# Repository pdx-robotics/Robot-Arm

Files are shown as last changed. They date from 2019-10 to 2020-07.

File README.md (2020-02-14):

# Robot-Arm
This repo is for the Robot Arm project by the Viking Robotics Society.

## Introduction
The idea of this project is to build a 5-DOF Robot Arm that will be able to draw and manipulate tasks. This project is set out to be completed by the end of the Winter Term 2020. A backup deadline is Spring 2020.

## Terminology

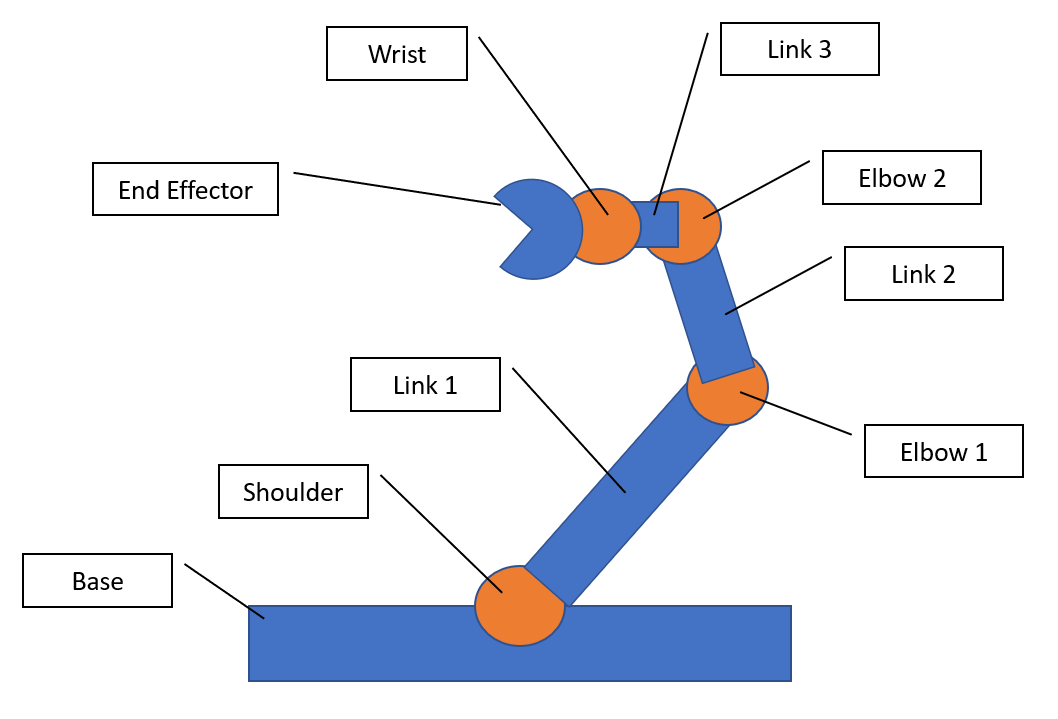
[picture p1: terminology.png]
Robot Arm Terminology


## Current Progress

Version 2

Version 2

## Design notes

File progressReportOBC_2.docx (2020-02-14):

To: OBC Committee

From: Viking Robotics Society

Subject: Robot Arm – Progress Report 2

Dear OBC Committee,

The following letter is to report on the progress of the Robot Arm project that is due at the end of Spring

term 2020.

Project website: https://pdx-robotics.github.io/Robot-Arm/

Introduction

On November 01, 2019, we have submitted the project proposal for designing a Robotic Arm for the

Viking Robotics Society. Upon receiving approval for the project, we have immediately started working

on designing the CAD model and planning for the project. The goal is to build a fully functional robotic

arm that can draw and write from human user input. The project is currently being worked on by the

members of VRS until the final submission.

The Background

VRS does not have a working robot that is designed and programmed by the members from scratch. All

of our previous projects have been from pre-built kits. We currently have several members who are

seniors and very invested in learning more about robotics. This project is initiated to give the members the

opportunities to learn more about the engineering design process and nurture a new generation of new

members about project management and teamwork. This project will also give the club something to

show off that is of our own design.

Work Completed

Physical Design

We have completed the second design of the robot arm, which has been 3D printed. However, this current design is too heavy to perform smooth motions; the next design aims at reducing the weight and improve the rigidity of the joints.

Electronics

We have assembled the Dynamixel motors and performed torque tests to evaluate their functionality. The AX12’s perform as expected. The RX64 is using an obsolete communication protocol that does not have sufficient documentation. We have consulted with Professor Alexander Hunt, who works with Dynamixels in his research. Dr. Hunt said that he has never worked on the old protocol in his line of work, given many years of experience with Dynamixel. We will need to order a new motor that uses the lastest communication protocol for the robot arm project.

Show & tell

Video

Link 1 (https://www.youtube.com/watch?v=8Y9AhXR_reE)

Link 2 (https://www.youtube.com/watch?v=c67NiDEWrtY)

Picture

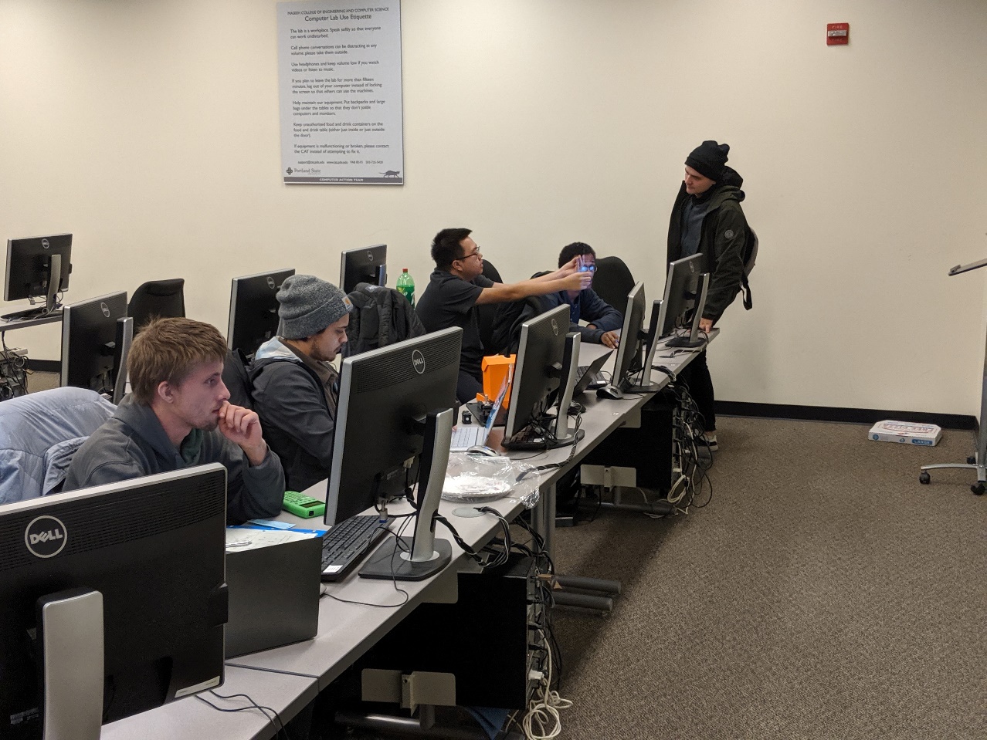
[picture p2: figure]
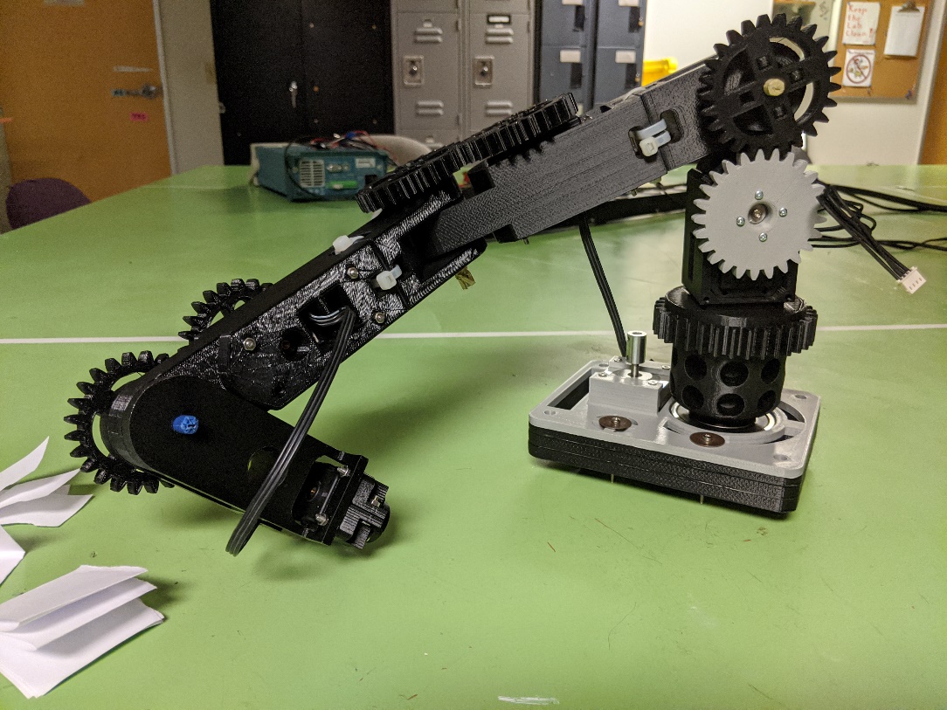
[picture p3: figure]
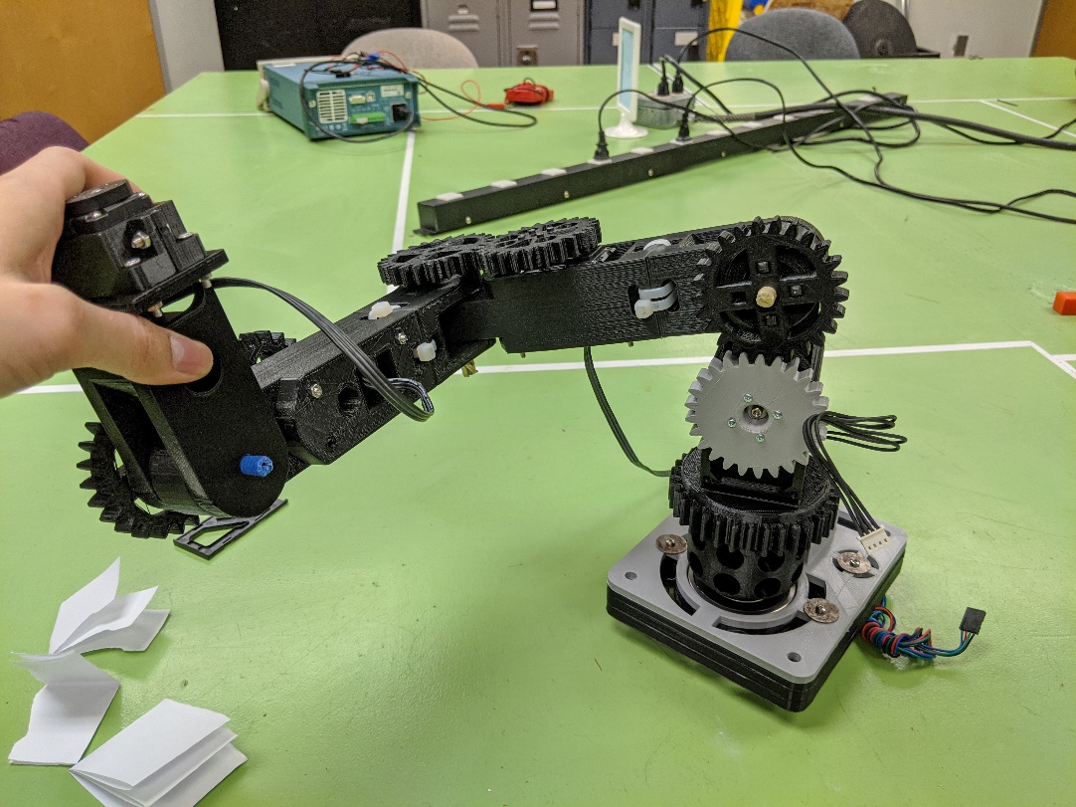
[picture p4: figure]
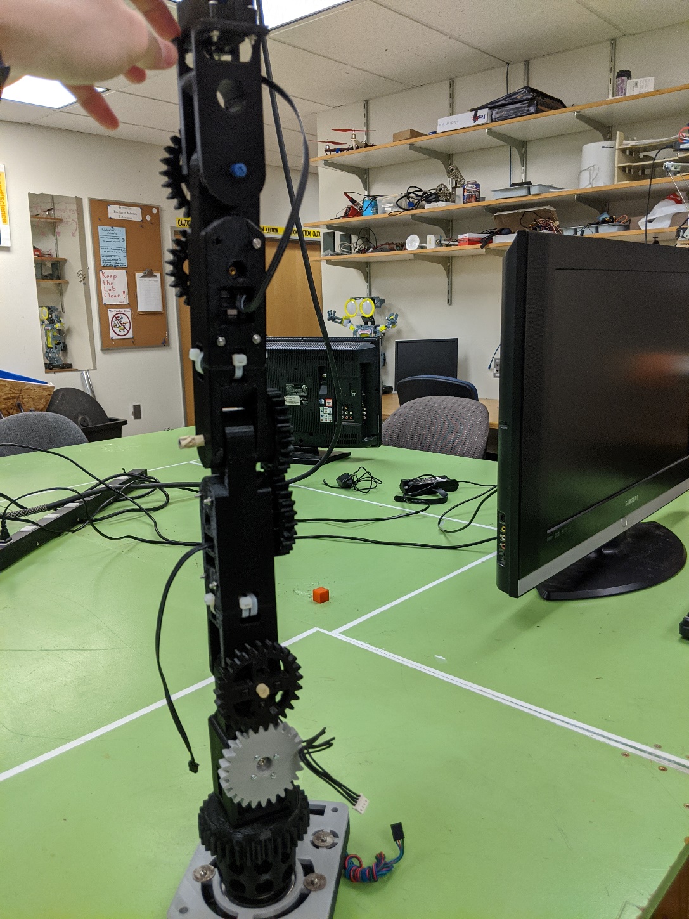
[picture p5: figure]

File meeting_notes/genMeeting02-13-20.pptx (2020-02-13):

## Robot Arm Update

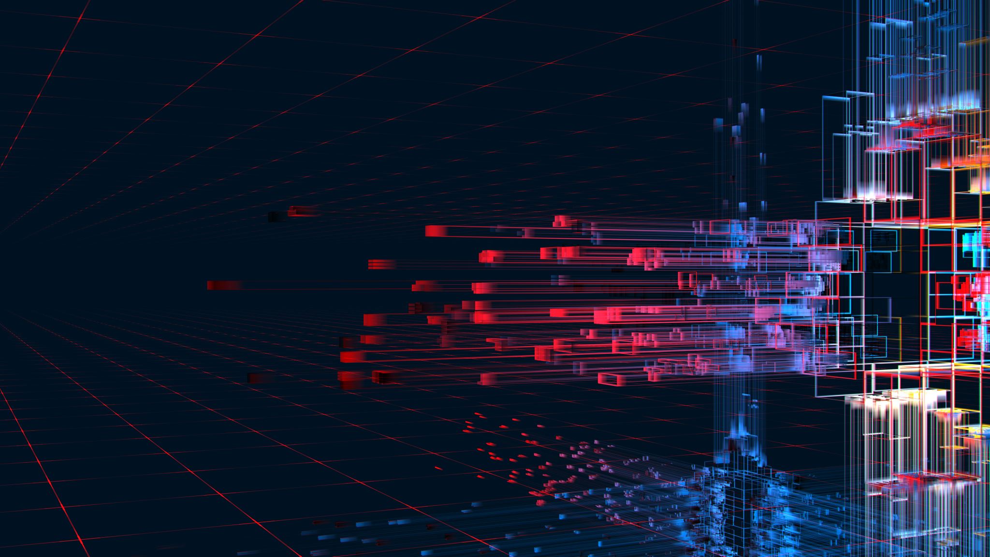
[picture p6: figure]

Viking Robotics Society

## Update from the programming team

- Issues?
- Roadblock?
- How’s the CM700 board? Did you make an progress on it?

## Update for the base redesign

- Is it print-ready?
- Any issues?

## Current arm

- The base shaft fractured. We will have to reprint it.

## Timeline revisiting

- The base redesign needed to be done by the end of this term.
- Might need to rethink the timeline for the programming group.

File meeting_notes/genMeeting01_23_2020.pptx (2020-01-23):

## Robot arm weekly meeting

Viking Robotics Society
Thursday 01-16-2020

## Current Progress

- We did things.
- The AX12 can move the base around.
- We got the RX64 to work. It spins around
- The term is getting busy, if you need to take a break to do your school stuff, you are more than welcome to.

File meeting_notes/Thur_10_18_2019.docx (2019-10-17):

Thursday, October 10, 2019 @ 5:00pm

Review of previous meeting:

- Github training
- Any question about Github or deadlines?

Goals for today meeting:

- Welcome our technical adviser, updates on current progress.

Agenda:

- Current progress of the arm:
  - Finished the base design
  - Finished Shoulder Gear
- Give the Cody our current overall design of the arm
  - Feedback from Cody?

Question?

Next meeting?

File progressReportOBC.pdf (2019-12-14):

To: OBC Committee

From: Viking Robotics Society

Subject: Robot Arm – Progress Report

Dear OBC Committee,

The following letter is to report on the progress of the Robot Arm project that is due at the end of Spring term 2020.

Introduction

On November 01, 2019, we have submitted the project proposal for designing a Robotic Arm for the Viking Robotics Society. Upon receiving approval for the project, we have immediately started working on designing the CAD model and planning for the project. The goal is to build a fully functional robotic arm that can draw and write from human user input. The project is currently being worked on by the members of VRS until the final submission.

The Background

VRS does not have a working robot that is designed and programmed by the members from scratch. All of our previous projects have been from pre-built kits. We currently have several members who are seniors and very invested in learning more about robotics. This project is initiated to give the members the opportunities to learn more about the engineering design process and nurture a new generation of new members about project management and teamwork. This project will also give the club something to show off that is of our own design.

Work Completed

We have completed the second iteration of the arm design and we are currently printing out more parts to start the assembly. We have also received several servos and parts that we ordered. A team is currently working on the communication and electronics of the arm. We have also been in constant contact with the Agile and Adaptive Robotics Lab graduate student to get help with the technical and challenges that we encountered in the process.

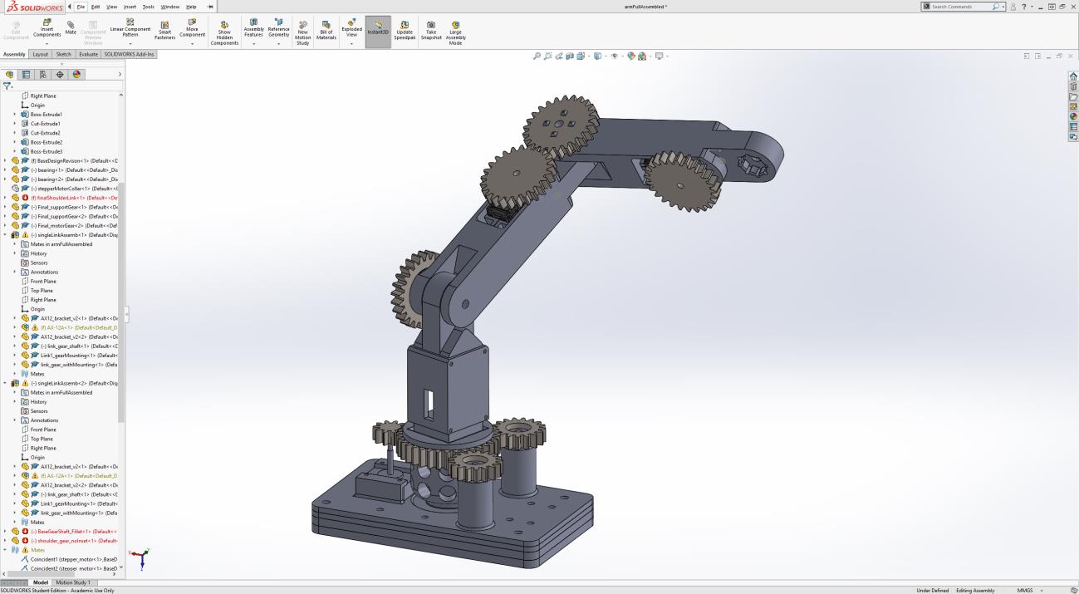
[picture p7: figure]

Work to Be Completed

We plan to have the full assembly by the end of the Winter Break; this will be the second version of the arm. During the Winter term and Spring term, the software team can start working on the programming of the arm, while the design team will work on the electronics and continuously making improvements upon the current model. We also plan to show off our current progress at the Robotics Club game night to recruit more members to help with the project.

Anticipated Problems

One of the servos that we ordered on November 12, 2019, has not shown up. We plan to have the full assembly to be completed during the Winter break. If we do not get the servo in time, the deadline for the project will be delayed. Additionally, the OBC committee will not be available during the break, which makes ordering replacement for the servo will be significantly challenging. I have contacted the advisor of the club to look into this issue and make sure that we will get the part in time.

The 3D printer of the club is degrading. It has broken down many times when we tried to print the parts. The parts have also been warping much more significantly than normal, which causes fitting to be challenging. We are designing our model to be 3D-printing friendly, but without a good printer, it is taking significantly longer to get parts. We will have to work with what we have. We will try to maintain the printer and fix it if necessary.

Conclusion

Based on the current progress, we should have the project to be completed at the end of the Spring term 2020. Despite several delays in our timeline, we are still on schedule. We plan to order several more parts that we have missed in the last order to support the project.

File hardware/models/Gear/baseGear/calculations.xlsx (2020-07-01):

Driving gear calculation for the bas
 | d (pich diameter) mm | 58.3
 | N (number of teeth) | 11
 | a (Addendum) | 5.3 | Addendum Circle | 63.6
 | b (Dedendum) | 6.625 | Dedendum Circle | 51.675
 | m (mod) | 5.3 | Base Circle | 59.76445068
 | P (diametral pitch) | 0.1886792453 | Pitch Circle | 58.3
 | hk (working depth) | 11.925

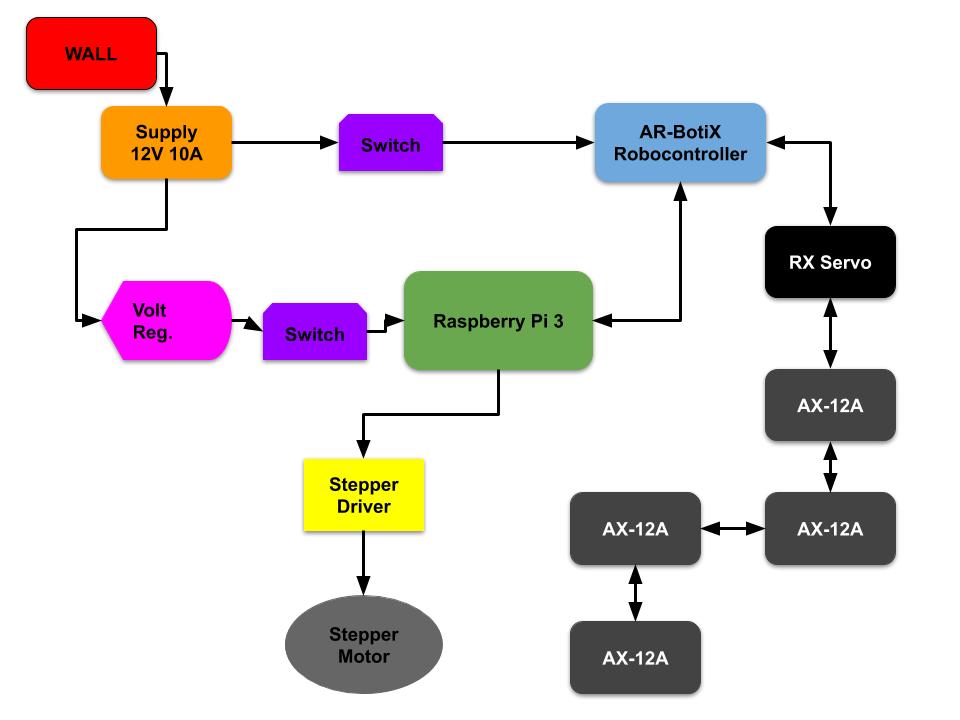
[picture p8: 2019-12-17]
Electronics Schematics/VRS_Arm_CircuitOutline.jpg

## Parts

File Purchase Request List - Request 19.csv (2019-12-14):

Click to return to INDEX | Viking Robotics Society
Provide a backup purchase link for all purchases. Requests take a while to process and parts may run out of stock during the process
Budget Request #: | 19 | Date Submitted: | 12/2/2019 | Date Approved: | WIP
Notes | This budget request is for VRS game night |  |  | Amount Approved: | $0.00
 |  |  | Preferred Purchase Option |  |  |  |  |  |  | Backup Purchase Option
Reason for Purchase | Items | Notes | Count in one order | # of orders to get | Cost per order | S&H | Total w/ S&H | Link | Notes | Count in one order | # of orders to get | Cost per order | S&H | Total w/ S&H | Link | Notes
Overall Total |  |  |  |  |  | $13.15 | $185.53 |  |  | Overall Total |  |  | $0.00 | $0.00
Robot Arm project | CM-700 Robot Controller |  | 1 | 1 | $119.90 | $13.15 | $133.05 | https://www.trossenrobotics.com/store/p/6410-CM-700-Robotis-Servo-Controller.aspx
Robot Arm project | LN-101 USB Downloader |  | 1 | 1 | $14.90 | $0.00 | $14.90 | https://www.trossenrobotics.com/store/p/6322-LN-101-USB-Downloader.aspx
Robot Arm project | Filament 1.75mm - Black |  | 1 | 1 | $17.59 | $0.00 | $17.59 | https://www.amazon.com/HATCHBOX-3D-Filament-Dimensional-Accuracy/dp/B00J0ECR5I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
Robot Arm project | Filament 3.00mm - Yellow |  | 1 | 1 | $19.99 | $0.00 | $19.99 | https://www.amazon.com/HATCHBOX-3D-Filament-Dimensional-Accuracy/dp/B019EFB7Y4?s=industrial

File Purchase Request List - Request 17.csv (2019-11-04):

Click to return to INDEX | Viking Robotics Society
Provide a backup purchase link for all purchases. Requests take a while to process and parts may run out of stock during the process
Budget Request #: | Request 17 | Date Submitted: | 10/28/2019 | Date Approved: | 11/01/2019
Notes | This purchase request is for the Robot Arm project |  |  | Amount Approved: | $510.50
 |  |  | Preferred Purchase Option |  |  |  |  |  |  | Backup Purchase Option
Reason for Purchase | Items | Notes | Count in one order | # of orders to get | Cost per order | S&H | Total w/ S&H | Link | Notes | Count in one order | # of orders to get | Cost per order | S&H | Total w/ S&H | Link | Notes
Overall Total |  |  |  |  |  | $24.46 | $510.50 |  |  | Overall Total |  |  | $0.00 | $0.00
Robot Arm Project | Raspberry Pi 3 |  | 1 | 1 | $57.89 |  | $57.89 | https://www.amazon.com/ELEMENT-Element14-Raspberry-Pi-Motherboard/dp/B07P4LSDYV
Robot Arm Project | Ar-BotiX-M Robo Controller |  | 1 | 1 | $39.95 |  | $39.95 | https://www.trossenrobotics.com/p/arbotix-robot-controller.aspx
Robot Arm Project | Stepper Motor Controller |  | 5 | 1 | $9.99 |  | $9.99 | https://www.amazon.com/KINGPRINT-DRV8825-Stepper-Driver-Printer/dp/B075XH1TSJ?s=industrial
Robot Arm Project | Dynamixel AX-12A Digital Servos |  | 1 | 2 | $44.90 | $13.14 | $102.94 | https://www.trossenrobotics.com/dynamixel-ax-12-robot-actuator.aspx
Robot Arm Project | Dynamixel Cables |  | 10 | 1 | $14.90 |  | $14.90 | https://www.trossenrobotics.com/p/250mm-3-pin-dynamixel-compatible-cables-10-pack
Robot Arm Project | Power Supply |  | 1 | 1 | $21.99 |  | $21.99 | https://www.amazon.com/Xenocam-Power-Supply-Splitter-Cameras/dp/B07X5LQ17L
Robot Arm Project | Dynamixel RX |  | 1 | 1 | $195.93 | $3.32 | $199.25 | http://www.robotis.us/dynamixel-rx-64-hn05-n1/
Robot Arm Project | 3D printing filament |  | 1 | 1 | $19.99 |  | $19.99 | https://www.amazon.com/HATCHBOX-3D-Filament-Dimensional-Accuracy/dp/B00J0ECR5I
Robot Arm Project | Bearing |  | 1 | 1 | $35.60 | $8.00 | $43.60 | https://www.mcmaster.com/2349K425

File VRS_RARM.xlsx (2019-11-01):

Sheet: RESOURCES
RESOURCES | LINK
How - To | https://www.raspberryturk.com/details/arm/python-dynamixel.html
Stepper Motor | https://www.youtube.com/watch?v=5CmjB4WF5XA

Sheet: Electronics BOM
ITEM | QUANTITY | LINK | COST ($) Individual | In Inventory
Raspberry Pi 3 | 1 | https://www.amazon.com/ELEMENT-Element14-Raspberry-Pi-Motherboard/dp/B07P4LSDYV | 51.89 | NO
Ar-BotiX-M Robo Controller | 1 | https://www.trossenrobotics.com/p/arbotix-robot-controller.aspx | 39.95 | NO
Stepper Motor Controller | 1 | https://www.amazon.com/KINGPRINT-DRV8825-Stepper-Driver-Printer/dp/B075XH1TSJ?s=industrial |  | NO
Dynamixel AX-12A Digital Servos | 2 | https://www.trossenrobotics.com/dynamixel-ax-12-robot-actuator.aspx | 44.9 | NO
JK42HS48 - 1604A | 0 | https://www.amazon.com/STEPPERONLINE-Stepper-Bipolar-Connector-compatible/dp/B00PNEQKC0 | 13.99 | YES
Dynamixel Cables | 1 | https://www.trossenrobotics.com/p/250mm-3-pin-dynamixel-compatible-cables-10-pack | 14.9 | NO
Power Supply | 1 | https://www.amazon.com/Xenocam-Power-Supply-Splitter-Cameras/dp/B07X5LQ17L | 21.99 | NO
Dynamixel RX | 1 | http://www.robotis.us/dynamixel-rx-64-hn05-n1/ | 195.33 | NO

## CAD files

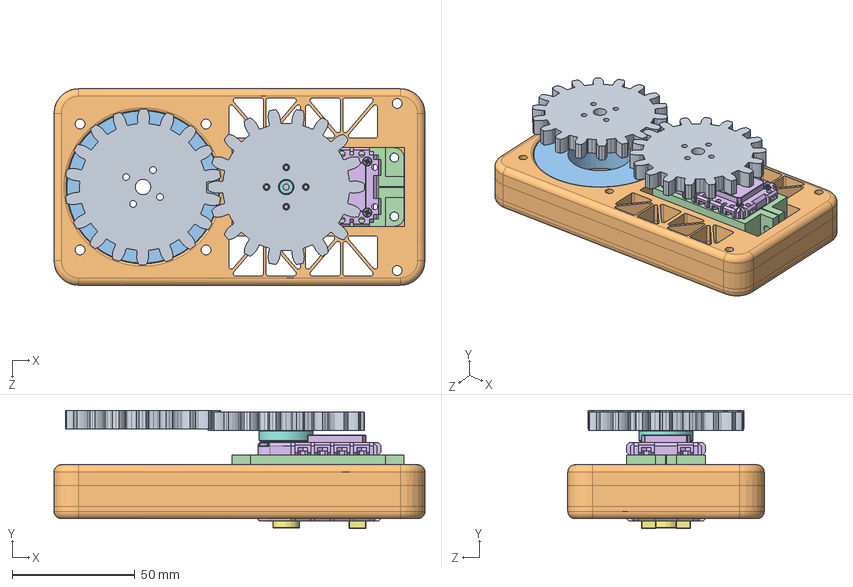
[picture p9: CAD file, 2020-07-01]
hardware/models/assembledArm/assemblyCheck/fullAssembly_v2.SLDASM
151.0 x 48.1 x 80.0 mm
baseGear x 2
base_v2
largeBearing
AX12_bracket_v2 x 2
AX-12A-01
AX-12A-02
AX-12A-03
AX-12A-04
SetScrew x 4

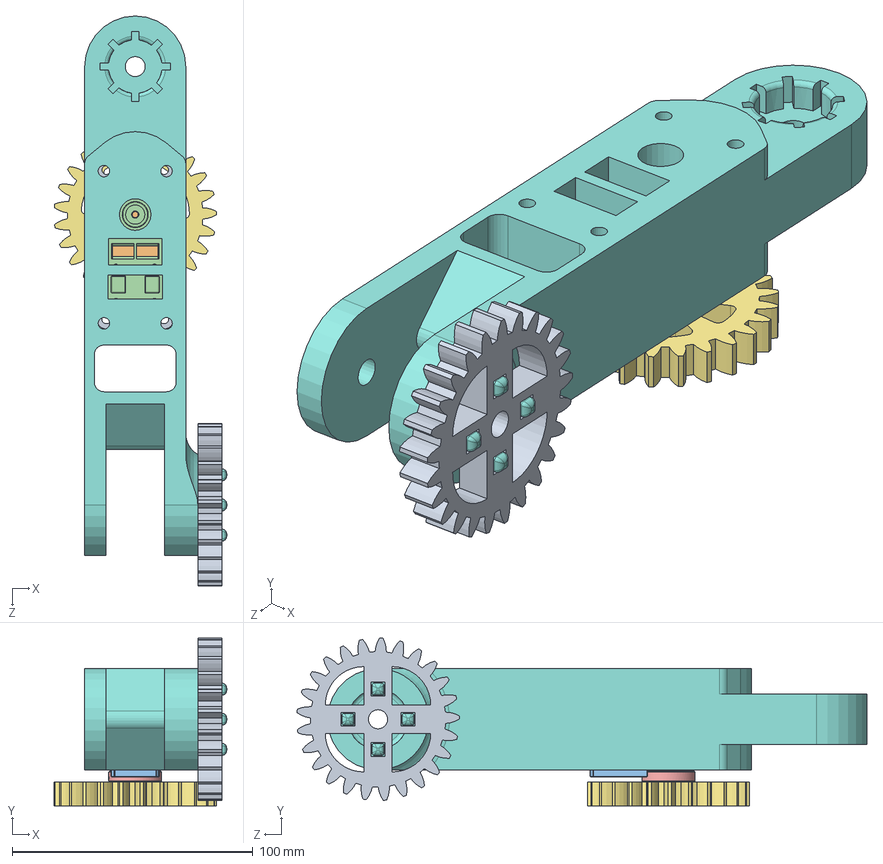
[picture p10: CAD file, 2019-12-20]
hardware/models/assembledArm/link_1_2/singleLinkAssemb.SLDASM
71.6 x 69.7 x 236.6 mm
AX12_bracket_v2 x 2
AX-12A-01
AX-12A-02
AX-12A-03
AX-12A-04
SetScrew x 4
link_gear_shaft
Link1_gearMounting
link_gear_withMounting

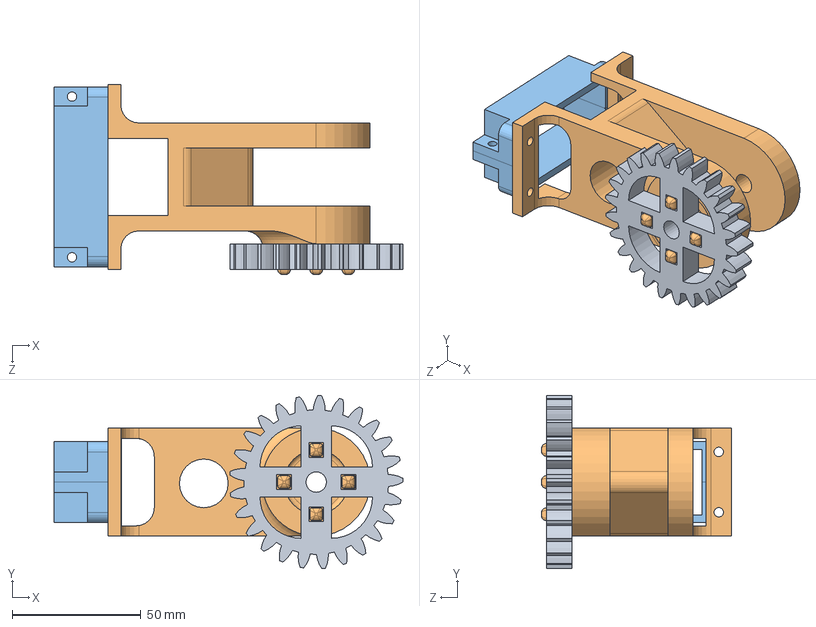
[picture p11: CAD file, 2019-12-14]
hardware/models/assembledArm/linkWrist/wristAssembly.SLDASM
135.7 x 67.4 x 74.0 mm
link_gear_withMounting
wristLinkRevision
AX12_bracket_v2 x 2

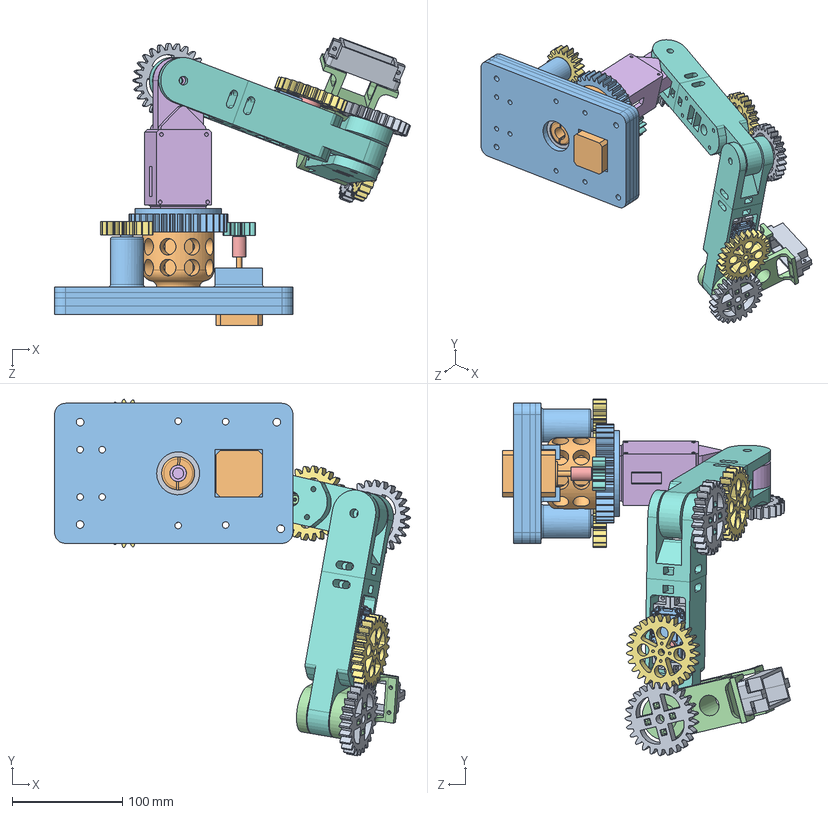
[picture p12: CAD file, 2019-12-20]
hardware/models/assembledArm/assemblyCheck/armFullAssembled.SLDASM
322.4 x 322.9 x 260.9 mm
largeBearing
stepper_motor
BaseDesignRevison
bearing x 2
finalShoulderLink
Final_supportGear x 2
Final_motorGear
AX12_bracket_v2 x 6
AX-12A-01 x 2
AX-12A-02 x 2
AX-12A-03 x 2
AX-12A-04 x 2
SetScrew x 8
link_gear_shaft x 2
Link1_gearMounting x 2
link_gear_withMounting x 3
BaseGearShaft_Fillet
shoulder_gear_noInset
wristLinkRevision

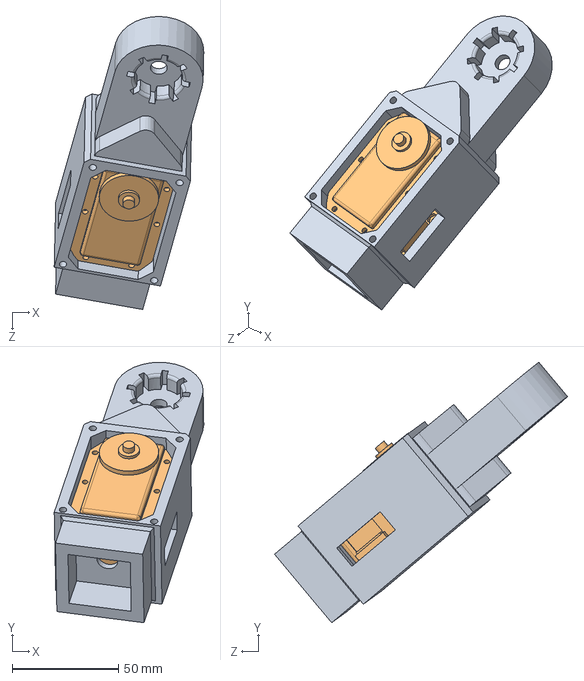
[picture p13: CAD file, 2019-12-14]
hardware/models/assembledArm/linkShoulder/assemShoulderLinkRX64.SLDASM
70.4 x 122.6 x 137.9 mm
linkShoulder
rx64N

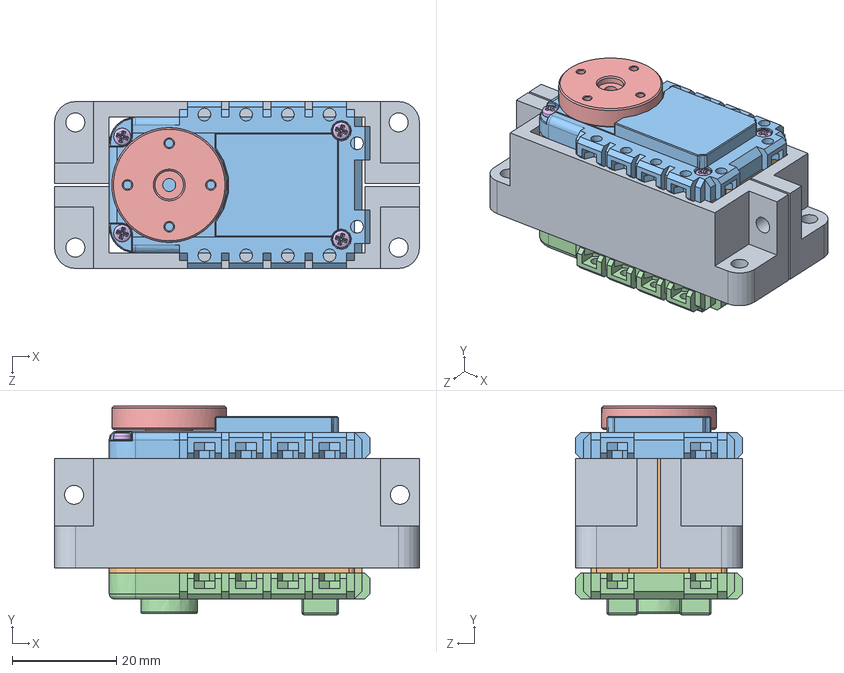
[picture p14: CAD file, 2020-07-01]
hardware/models/assembledArm/motorAX12/A12_bracket_subassm.SLDASM
70.0 x 40.0 x 32.0 mm
AX12_bracket_v2 x 2
AX-12A-01
AX-12A-02
AX-12A-03
AX-12A-04
SetScrew x 4

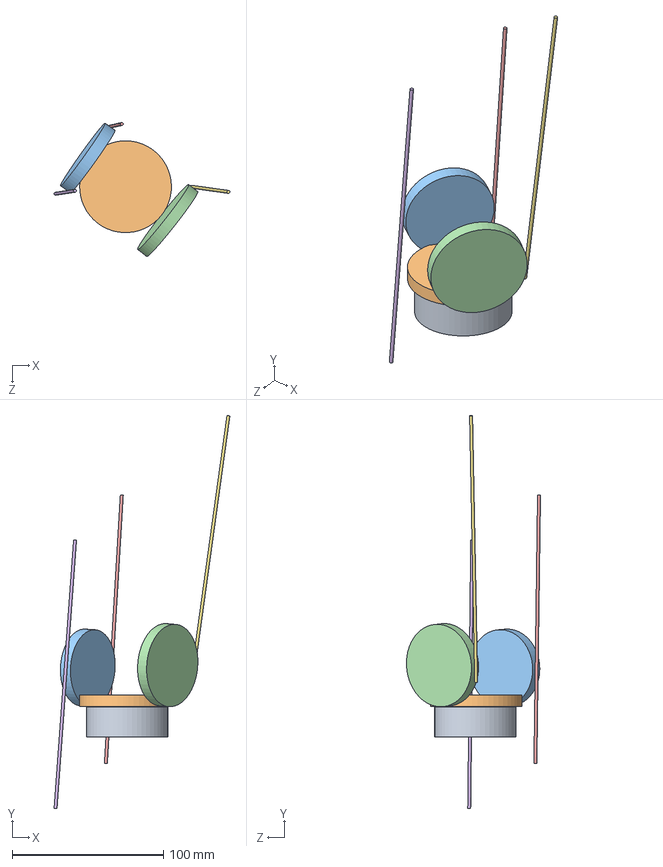
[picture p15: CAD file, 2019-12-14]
hardware/models/endEffector/threePenCycleMechanism/Triple Pen.SLDASM
116.2 x 259.7 x 88.6 mm
DC Motor Cavity
Gear 1
Gear 2
Gear 3
Pen 1
Pen 2
Pen 3

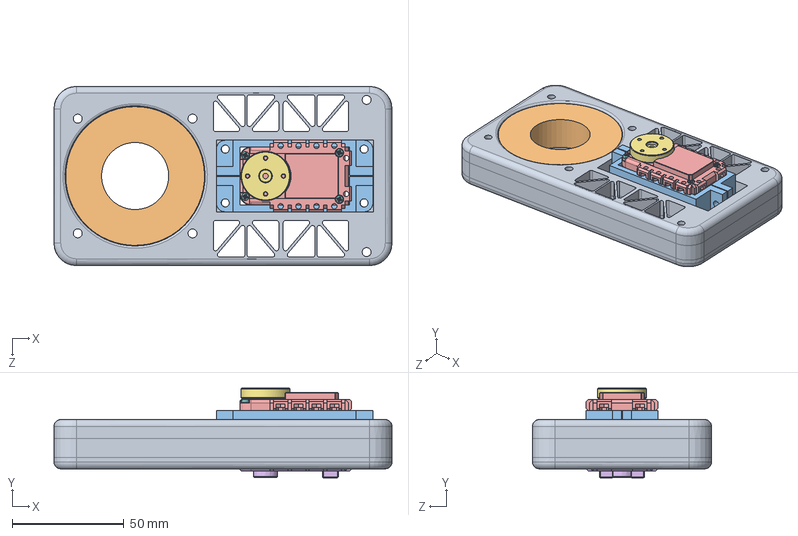
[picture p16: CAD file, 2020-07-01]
hardware/models/assembledArm/base/baseBracketSubAssm.SLDASM
151.0 x 40.0 x 80.0 mm
base_v2
largeBearing
AX12_bracket_v2 x 2
AX-12A-01
AX-12A-02
AX-12A-03
AX-12A-04
SetScrew x 4

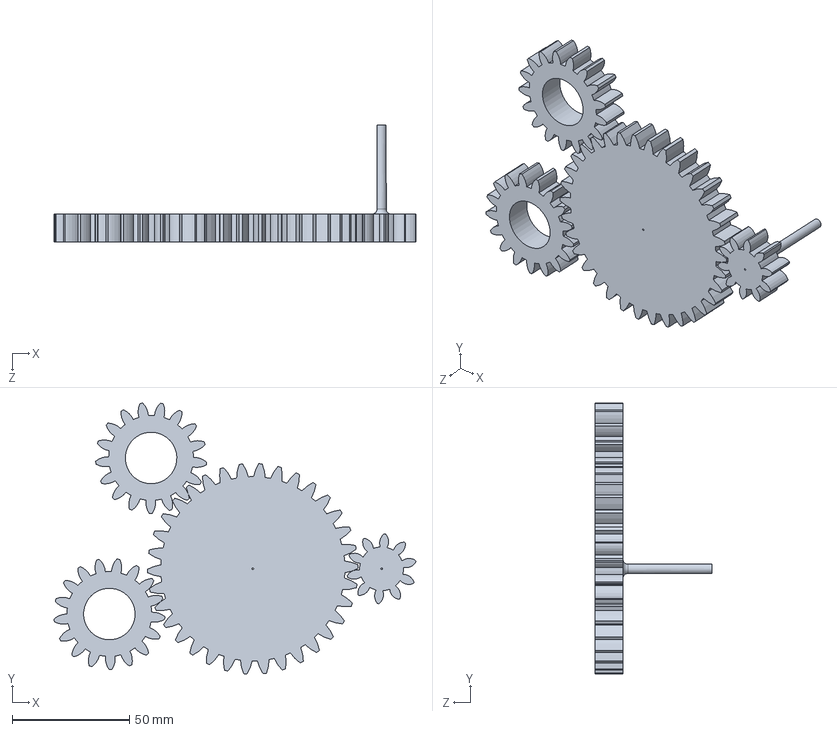
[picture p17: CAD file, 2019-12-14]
hardware/models/Gear/Final_supportGear_motorGear.SLDASM
154.7 x 115.8 x 50.0 mm
spur gear_am x 4

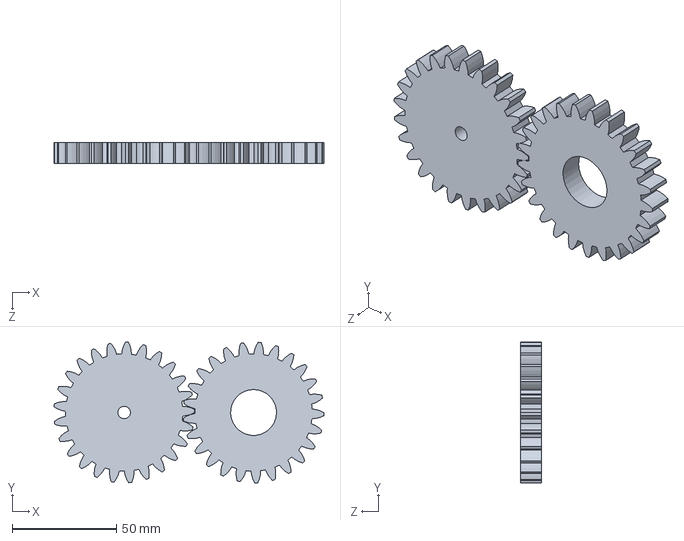
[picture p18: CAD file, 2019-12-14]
hardware/models/Gear_Link/link_gear.SLDASM
129.4 x 67.5 x 10.0 mm
spur gear_am x 2

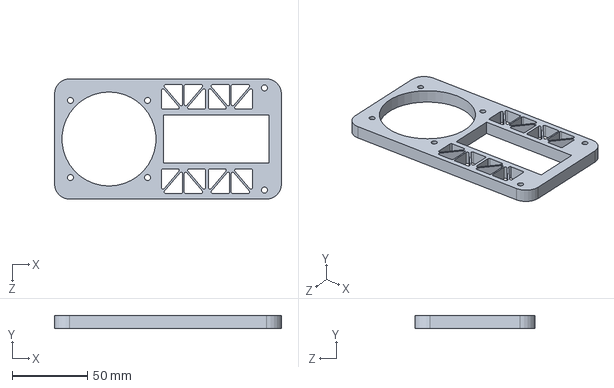
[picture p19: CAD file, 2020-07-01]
hardware/models/assembledArm/base/newBase_p1.sldprt
151.0 x 8.50 x 80.0 mm

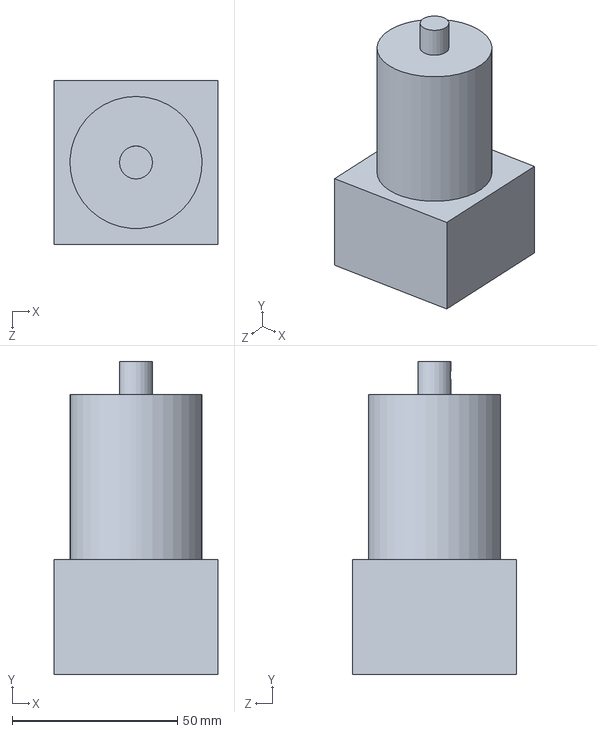
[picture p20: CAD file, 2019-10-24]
hardware/models/assembledArm/end_effector/endeffectorattachment.SLDPRT
49.5 x 94.8 x 49.5 mm

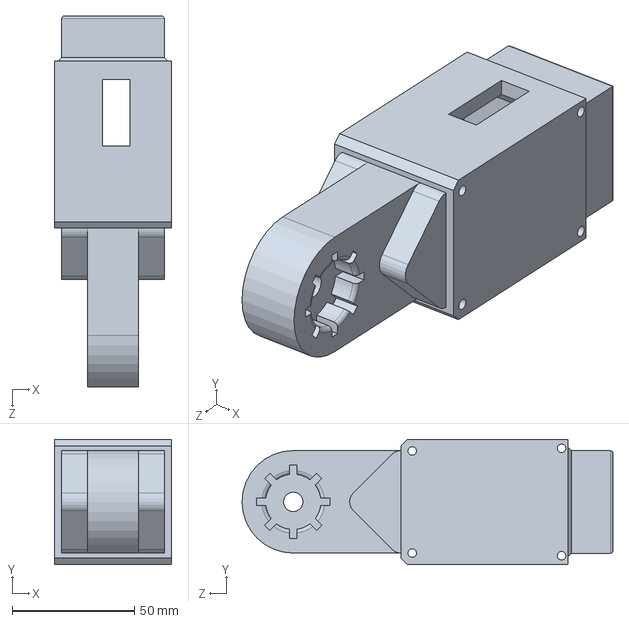
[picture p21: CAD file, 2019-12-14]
hardware/models/assembledArm/linkShoulder/finalShoulderLink.SLDPRT
48.0 x 51.2 x 152.0 mm

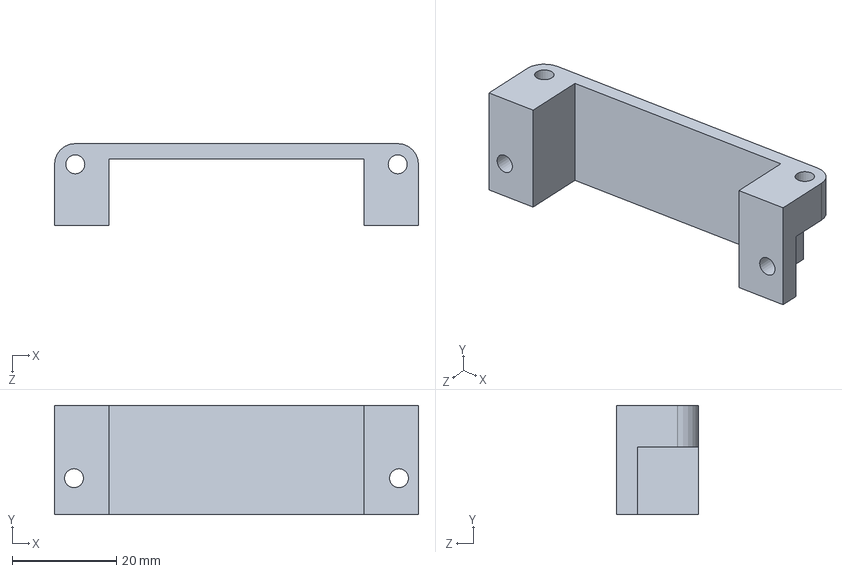
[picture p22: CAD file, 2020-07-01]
hardware/models/assembledArm/motorAX12/AX12_bracket_v2.SLDPRT
70.0 x 21.0 x 15.8 mm

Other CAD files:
hardware/models/assembledArm/gears/drivingGear.SLDPRT
hardware/models/assembledArm/motorStepper/stepperMotorCollar.SLDPRT
hardware/models/assembledArm/RX/bracketRx64.SLDPRT
hardware/models/assembledArm/shaftBase_Bearing/gearShafv2.SLDPRT
hardware/models/Gear/Final_motorGear.SLDPRT
hardware/models/Gear/Final_supportGear.SLDPRT
hardware/models/Gear/baseGear/baseGear.SLDPRT
hardware/models/Gear_Link/link_gear.SLDPRT
hardware/models/Gear_Link/link_gear_bearing.SLDPRT
hardware/models/Gear_Link/link_gear_shaft.SLDPRT
hardware/models/Gear_Link/link_gear_shoulder.SLDPRT
hardware/models/Gear_Link/link_gear_withMounting.SLDPRT
hardware/models/Gear_Shoulder/shoulder_gear_noInset.SLDPRT
hardware/models/Gear_Shoulder/shoulder_gear_original.SLDPRT
hardware/models/Motors&Accessories/CylinderV1.SLDPRT
hardware/models/Motors&Accessories/DYNAMIXEL_AX_12A/AX-12A-01.SLDPRT
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

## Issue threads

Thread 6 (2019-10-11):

Update new deadline 11/14/19 for the completion of the CAD model

jakechung42, 2019-10-11:
I have updated the deadline for the CAD model. Please let me know if we need to change this deadline.

jakechung42, 2019-10-11:
this issue can be closed when the deadline is met.

jakechung42, 2019-10-25:
The deadline is extended once again to November 14th. The CAD file of the first working version of the arm must be done by this day.

jakechung42, 2019-12-09:
CAD model iteration 2 is completed

Closed 2019-12-09.

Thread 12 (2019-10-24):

Dimension is really wacky

jakechung42, 2019-10-24:
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
The dimensions of the link in the arm is really wacky. Probably will have to rework this.

jakechung42, 2019-10-24:
This file is currently in my assembly branch. Send me a request if you want to pull it into your branch

jakechung42, 2019-10-25:
The dimension of the arm is supposed to be about 30% less. @Cr1sco

Closed 2019-12-09.

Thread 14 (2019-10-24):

the dimension on the shoulder gear is not correct

jakechung42, 2019-10-24:
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
Might need to re-dimension this gear.

jakechung42, 2019-10-28:
Need to investigate why the shoulder gear is off. The solidworks model makes it seem like it's bigger, but it's actually smaller when printed. Possible printing error.

VladislavRuchin, 2019-11-01:
I re-adjusted the dimensions of the shoulder and support gears by referring to the dimensions of the base.

Closed 2019-11-01.

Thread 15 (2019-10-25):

Joint do not allow for more than 190 degree rotation

Cr1sco, 2019-10-25:
The outer edge of arm links makes contact with the next link to prevent rotation.
Possible solution carving angles into the contact points to make for room to rotate into.

Closed 2019-12-09.

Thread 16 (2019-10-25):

Dimension of the Arm is wrong

Cr1sco, 2019-10-25:
The arm is roughly 30% larger than intended. Need to adjust most measurements

jakechung42, 2019-10-25:
#12 Close this issue, duplicated issue.

Closed 2019-10-25.

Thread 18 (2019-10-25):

SVG Transformation

JasonHolm, 2019-10-25:
We need to figure out how to transform a svg vector file into something that can causes the robot arm to move.

anthonybob, 2019-11-21:
This problem has been solved. I wrote a python script to extract the paths out of an SVG file. I am currently adding more functionality so my script will recognize all the different commands in an svg path. For example, the 'c' tag in an svg path is a bezier curve. The tag is followed by four coordinates. We can calculate an arbitrary amount of points of the curve from those four points using a recursive function.

Closed 2019-11-21.

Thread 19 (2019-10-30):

We are designing a new shoulder gear mechanism. Use a new bearing with ID 30mm and OD 62mm

jakechung42, 2019-10-30:
We are designing a new shoulder gear mechanism using the lazy suzy idea. We will use a giant bearing with ID 30 and OD 62mm on the base.

Closed 2019-12-09.

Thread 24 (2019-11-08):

joint gears design requirements

jakechung42, 2019-11-08:
I have the dimensions for the gears. The center to center diameter is 62mm. The gear ratio is 1:1. I will determine the inner shaft diameter later.

Closed 2019-12-09.

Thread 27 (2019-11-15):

things need to fix for final assembly

jakechung42, 2019-11-15:
- Make sure RX 64 fits
- adjust joint gear allignment.

jakechung42, 2019-12-09:
completed

Closed 2019-12-09.

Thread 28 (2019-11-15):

fix the dimension of the baseGearShaft

jakechung42, 2019-11-15:
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
The base gear shaft is currently interfering with the stepper motor. Need to fix its dimension before printing.

jakechung42, 2019-12-09:
Fixed the dimensions and designed a new base gear shaft

Closed 2019-12-09.

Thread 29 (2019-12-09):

Things to fix for iteration 3

jakechung42, 2019-12-09:
- Shave off excess material to make the arm lighter.
- fix tolerancing
- design the end effector

jakechung42, 2019-12-20:
@Cr1sco you can follow this list for rev. 3

VladislavRuchin, 2020-01-03:
According to my calculations, the infill for the links should be 55 percent if we want the motor to work properly.

jakechung42, 2020-01-08:
@VladislavRuchin noted.

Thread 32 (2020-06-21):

Redesign the base to fit a AX12

jakechung42, 2020-06-21:
Also lower the shaft to minimize the height of the center of mass.

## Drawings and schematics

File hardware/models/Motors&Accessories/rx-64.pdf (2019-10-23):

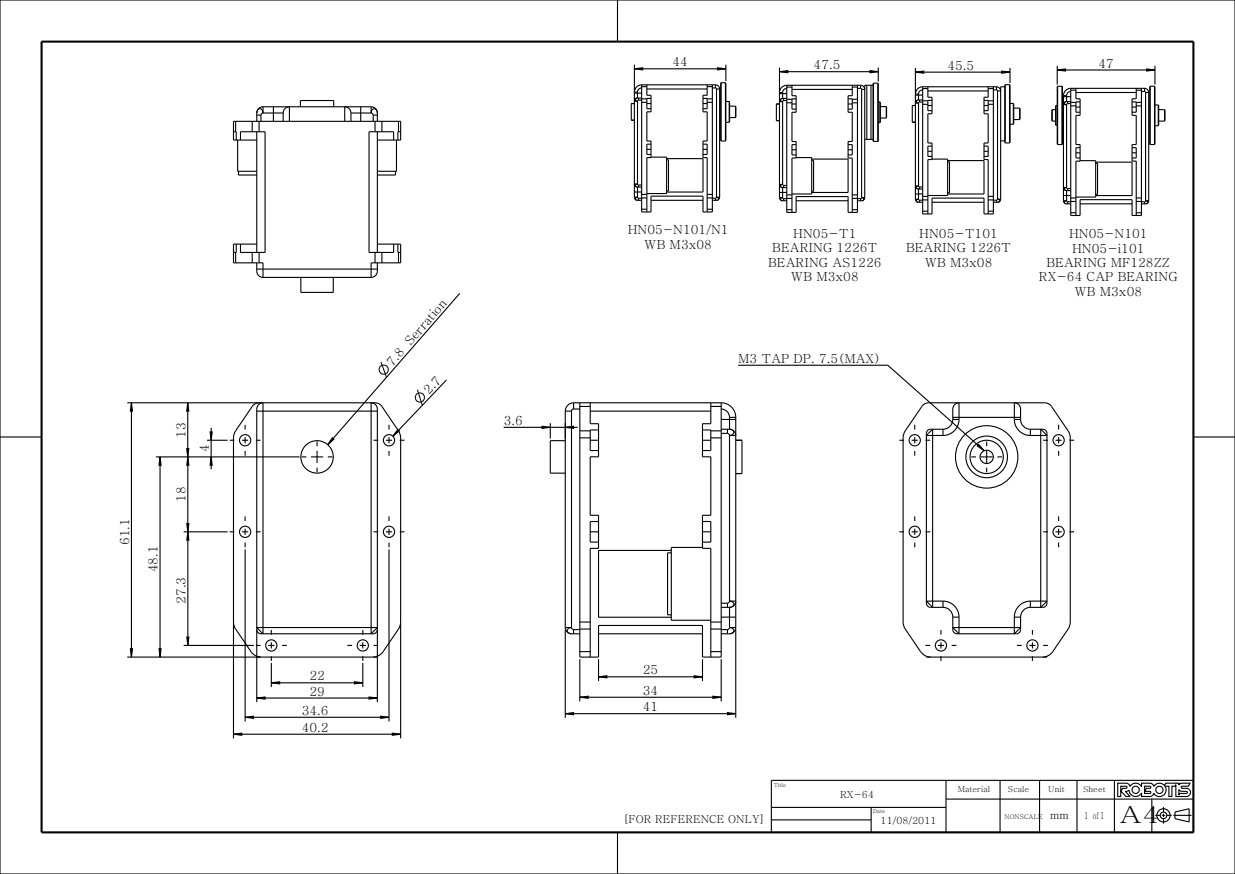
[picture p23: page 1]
NONSCALE; Serration 7.8; HN05-N101 HN05-i101 BEARING MF128ZZ RX-64 CAP BEARING WB M3x08; HN05-T101 BEARING 1226T WB M3x08; HN05-T1 BEARING 1226T BEARING AS1226 WB M3x08

M3 TAP DP. 7.5(MAX)

Title RX-64 | Material | Scale | Unit | Sheet

[FOR REFERENCE ONLY]

Date
mm | 1 of 1 11/08/2011

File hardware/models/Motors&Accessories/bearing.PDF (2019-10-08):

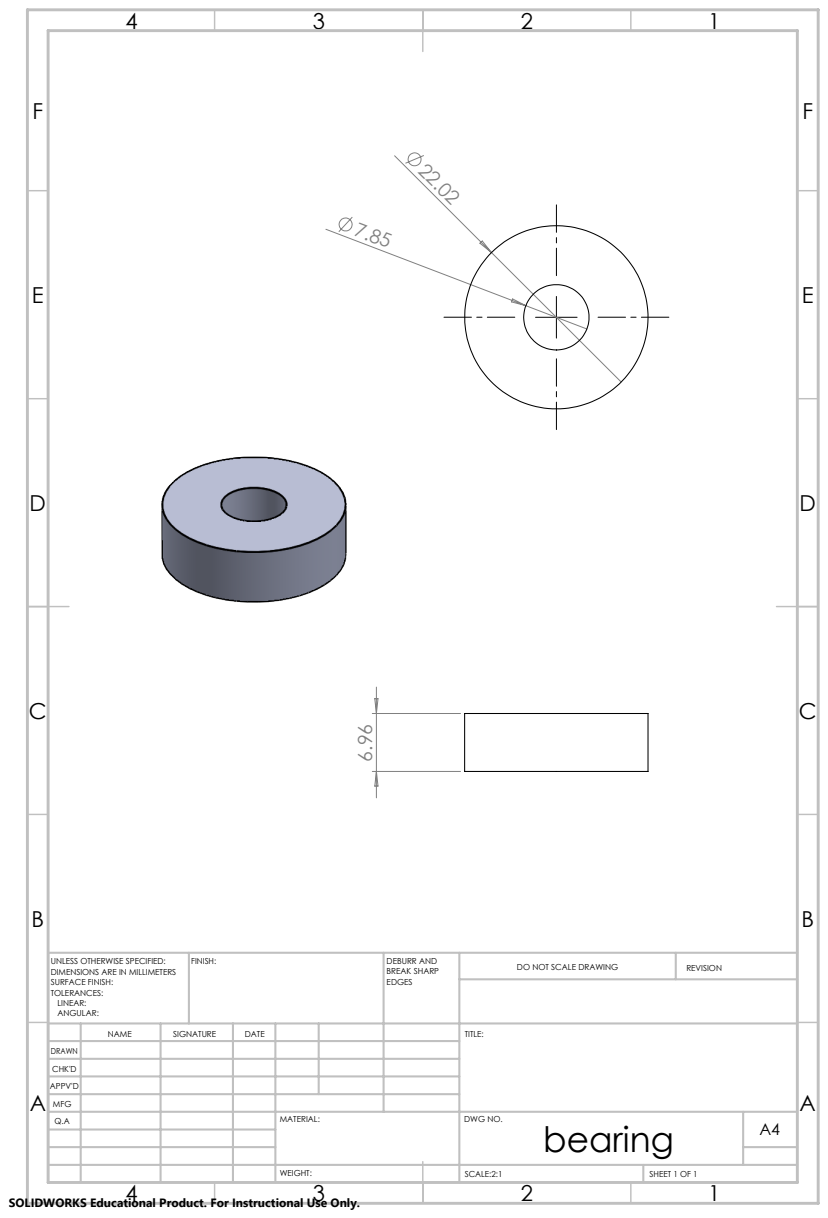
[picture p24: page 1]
FINISH:; DEBURR AND; BREAK SHARP; DO NOT SCALE DRAWING; REVISION; SCALE:2:1; SHEET 1 OF 1

UNLESS OTHERWISE SPECIFIED:
DIMENSIONS ARE IN MILLIMETERS
SURFACE FINISH:
TOLERANCES:
LINEAR:
ANGULAR:

NAME | SIGNATURE | DATE | | | | TITLE:

DRAWN
CHK'D
APPV'D
MFG
Q.A | | | | MATERIAL: | DWG NO. bearing | A4

SOLIDWORKS Educational Product. For Instructional Use Only.

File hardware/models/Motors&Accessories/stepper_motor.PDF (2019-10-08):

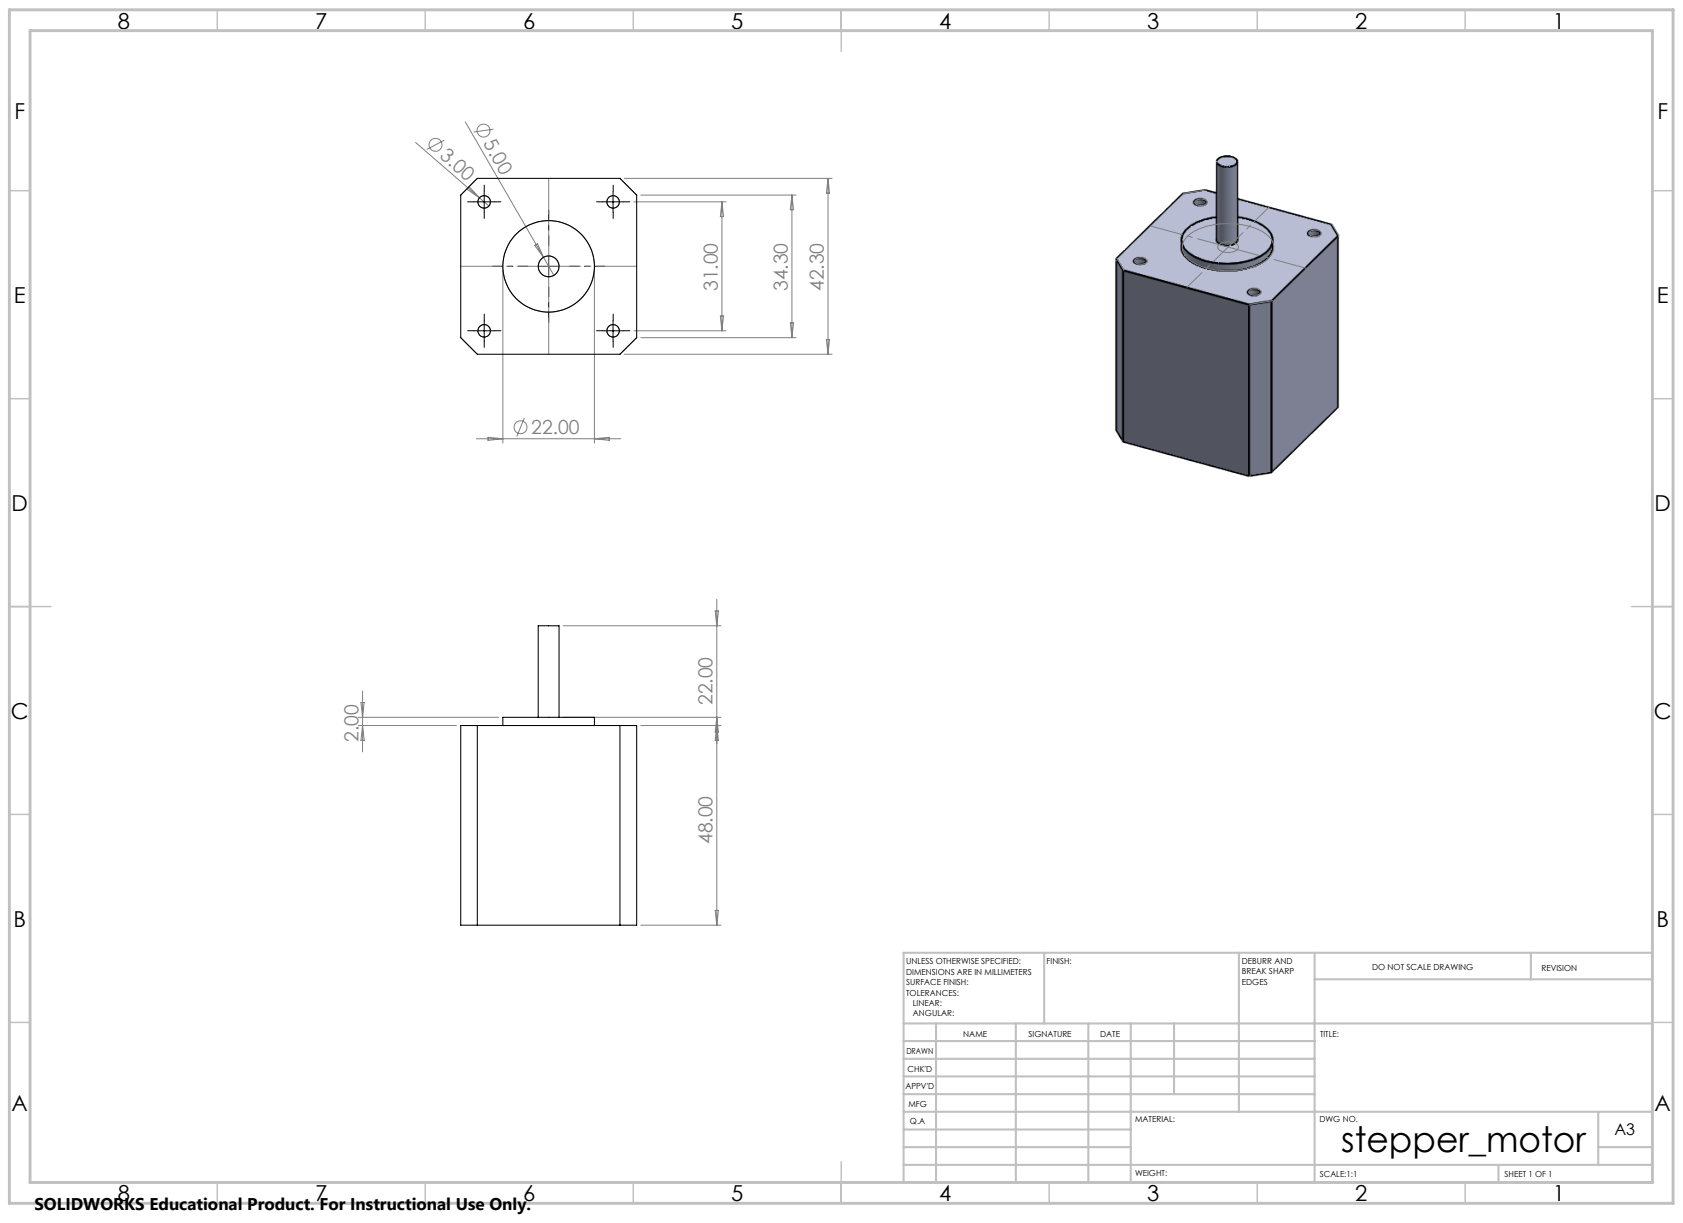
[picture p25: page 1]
FINISH:; DEBURR AND; BREAK SHARP; DO NOT SCALE DRAWING; REVISION; SCALE:1:1; SHEET 1 OF 1

UNLESS OTHERWISE SPECIFIED:
DIMENSIONS ARE IN MILLIMETERS
SURFACE FINISH:
TOLERANCES:
LINEAR:
ANGULAR:

NAME | SIGNATURE | DATE | | | | TITLE:

DRAWN
CHK'D
APPV'D
MFG
Q.A | | | | MATERIAL: | DWG NO. stepper_motor | A3

SOLIDWORKS Educational Product. For Instructional Use Only.

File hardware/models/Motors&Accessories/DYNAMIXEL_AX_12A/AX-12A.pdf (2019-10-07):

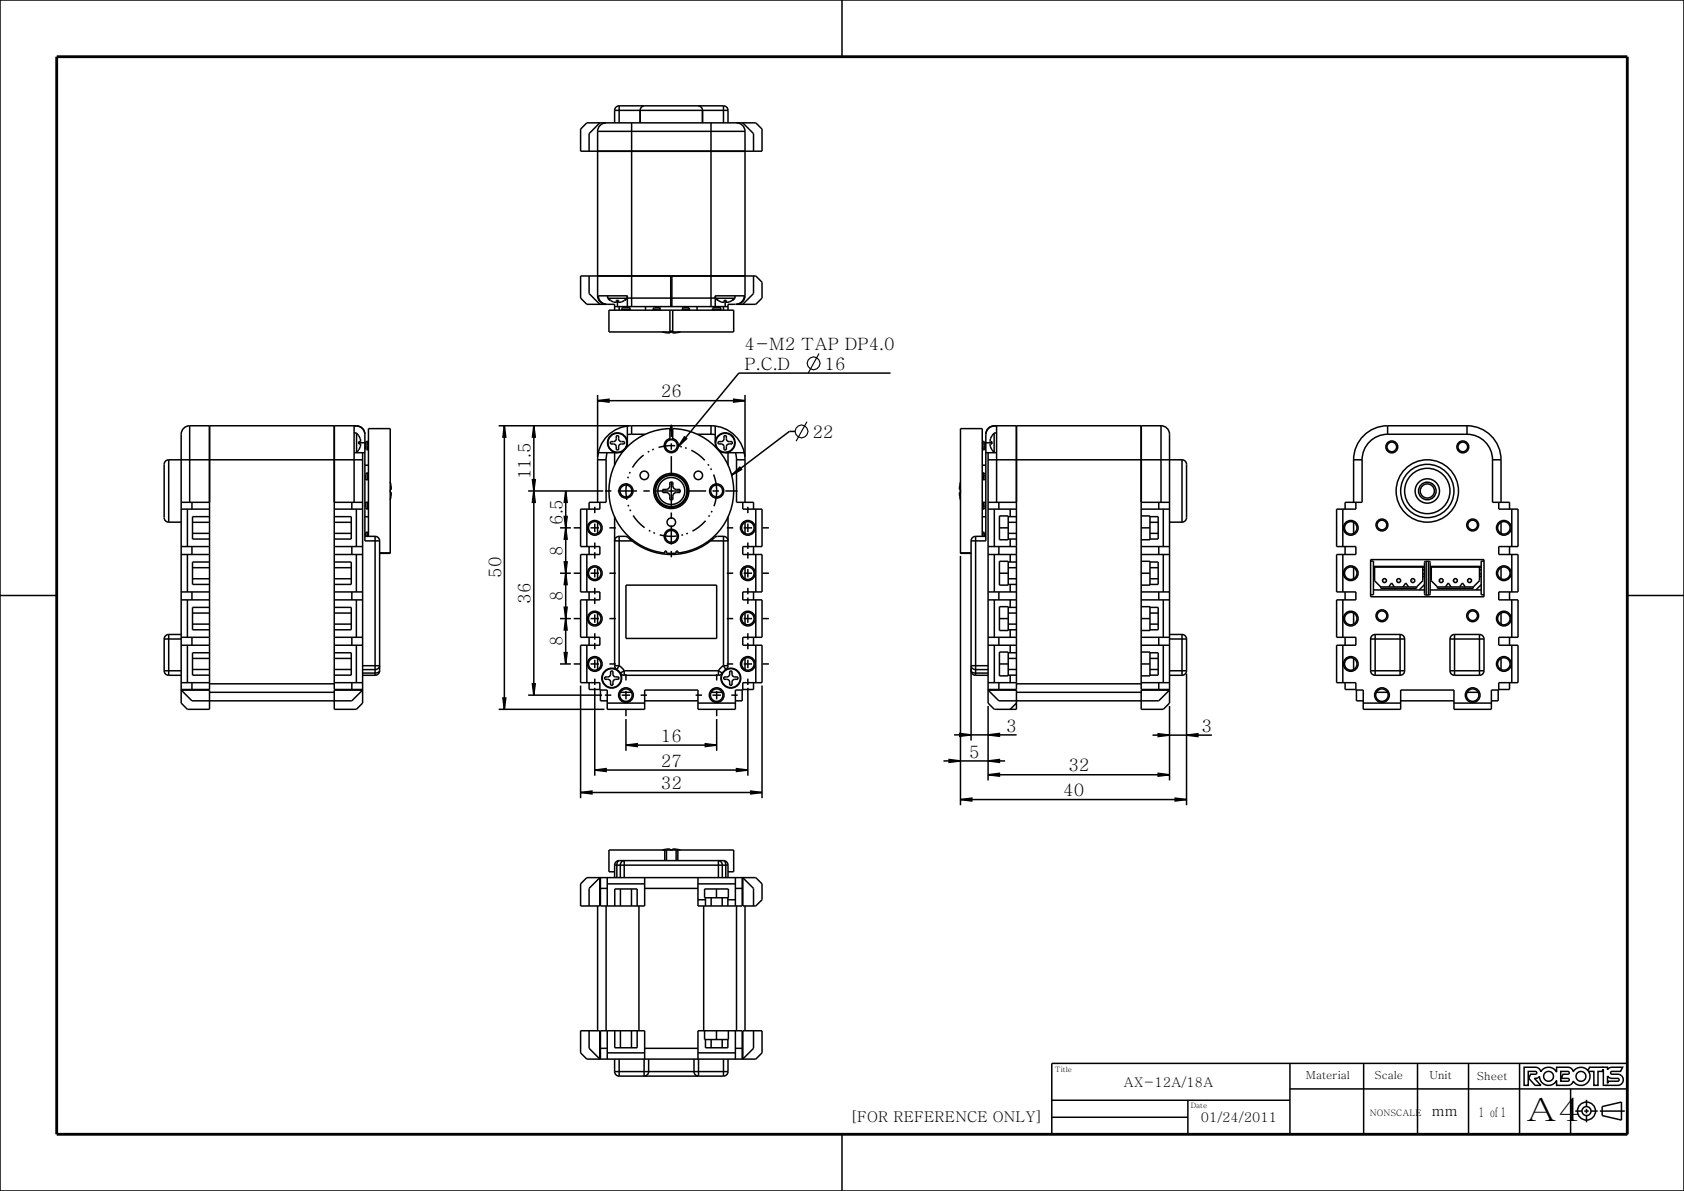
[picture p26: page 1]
NONSCALE; 4-M2 TAP DP4.0

Title AX-12A/18A | Material | Scale | Unit | Sheet

[FOR REFERENCE ONLY]

Date
mm | 1 of 1 01/24/2011

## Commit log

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2019-10-10 Revert "Merge branch 'master' of https://github.com/pdx-robotics/Robot-Arm"
    This reverts commit ed1a9b6e7c5a8753cac58669b746531b943dd12d, reversing
    changes made to 8c55fa5b6e13c9d38df2b1037fe93ada2a5dd486.
2019-10-10 Revert "Revert "Merge branch 'master' of https://github.com/pdx-robotics/Robot-Arm""
    This reverts commit 7b802af667b4e002f2cda44f6eb5b8eef7c5534a.
2019-10-10 Revert "Revert "Revert "Merge branch 'master' of https://github.com/pdx-robotics/Robot-Arm"""
    This reverts commit b6fe4b3ec8b61f6e6676e9199d32043ce2178678.
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2019-10-11 Revert " Base arm support system"
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2019-10-17 Here is the revised Base and drawing specification
    [BaseDesignRevison.SLDPRT, DesignSpecification.SLDDRW]
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2019-10-17 Here is the Shoulder link as well as the first link
    [Link1.SLDPRT, shoulderLink.SLDPRT]
2019-10-18 Worked on the links of the arm, did a couple of revision. Going to finish working on it in couple of days. Did an assembly to test the motion of the parts and its structural integrity.
    [Assem1.SLDASM, BaseDesignRevison.SLDPRT, Link1.SLDPRT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]
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2019-10-22 Shoulder_And_Support_Gears
    I created the shoulder and support gears using solidworks toolbox for spur gears.
    [Shoulder and Support Gears.SLDASM, Shoulder_and_Support_Gears.SLDASM]
2019-10-22 Upgrades
    The inner diameters and shafts were edited to match the dimensions of the base.
    [Shoulder_and_Support_Gears.SLDASM]
2019-10-22 add parts
    Modified base
    Reorganize the folder structure
    Add the links
    [Assem1.SLDASM, BaseDesignRevison.SLDPRT, DesignSpecification.SLDDRW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]
2019-10-23 Upgrading_Previous_Gears
    I updated the width of the shoulder gears. I also changed the format of the file so that Jake could work with it.
    [Shoulder and Support Gears.SLDPRT]
2019-10-23 Update Files
    I renamed the file so that others may edit the gears.
    [Shoulder_Gear_addon.SLDASM, Shoulder_Joint_System.SLDPRT, Shoulder_and_Support_Gears.SLDASM]
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2019-10-23 Servo Clamp Completed
    Finished design of link 1 and 2 servo clamp
    [AX-12A-01.SLDPRT, AX-12A-02.SLDPRT, AX-12A-03.SLDPRT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]
2019-10-23 Link for Gears
    A rough gear for the links was made.
    [linkgear.SLDPRT]
2019-10-23 Robot arm parts are assembled and completed in solidworks
    [Link1.SLDPRT, Link2.SLDPRT, endeffectorattachment.SLDPRT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]
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2019-11-01 Did More revision on the wrist, shoulder and the links.
    [Link1revision.SLDPRT, Link2.SLDPRT, shoulderLink.SLDPRT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]
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2019-11-02 11/1/2019 Work
    Changed the location of "CylinderV1"
    made changes to Base Gear Shaft where the bottom shaft was changed to 30mm as Johnathan requested
    [BaseGearShaft.SLDPRT, CylinderV1.SLDPRT, Robotic Arm Project Part 2.SLDDRW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]
2019-11-06 Worked on dimension doing more update on thursday
    [shoulderLinkRevision.SLDPRT]
2019-11-06 worked on the bracket attachment on the link
    [Link1revision.SLDPRT]
2019-11-06 bracket to mount the AX12 on to the link
    [AX12_bracket.SLDPRT]
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2019-11-08 Thicker Base Gear
    I made the base gear thicker for the shaft to be inserted through it.
    [thick_midle_gear_revised.SLDASM, thick_midle_gear_revised.SLDPRT]
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2019-11-08 Base changes
    Seperated base into multiple slices
    Corrected base dimensions
    [BaseDesignRevison.SLDPRT, Body1.sldprt, Body2.sldprt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]
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2019-11-08 Robot arm - Worked on dimensions of the shoulder link and tried to make the bracket for the RX64
    [Rxblockmodel.SLDPRT, bracketRx64.SLDPRT, shoulderLinkRevision.SLDPRT]
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2019-11-13 I created the joint gear with the 1:1 ratio.
    [link_gear.SLDASM, link_gear.SLDPRT, linkgear.SLDPRT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]
2019-11-13 update dimensions
    update dimensions for the arm and add cutouts for cables
    [Link1revision.SLDPRT]
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2019-11-13 I seperate the gears for the base and the links.
    [motor_gear.SLDPRT, shoulder_gear.SLDPRT, support_gear.SLDPRT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]
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2019-11-13 I added a shaft to the motor gear. I expanded the inner diameter of the support gear.
    [V4_motor_gear_shaft.SLDPRT, V4_support_gear_revised.SLDPRT]
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2019-11-13 Completed the shoulder link, Wrist link and the Bracket for the RX64
    [bracketRx64.SLDPRT, linkShoulder.SLDPRT, robotArmSimulation.SLDASM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]
2019-11-15 Created a a mock up of the collar for the stepper motor of the base.
    [stepperMotorCollar.SLDPRT]
2019-11-15 Worked on the assembly of the links of the robot
    [robotArmAssembly.SLDASM, robotArmSimulation.SLDASM]
2019-11-15 The Support and Motor Gear are complete.
    I edited the support and motor gear because the dimensions were off.
    [V5_motorGear.SLDPRT, V5_support_motor_gears.SLDASM, V5_supportgear.SLDPRT]
2019-11-15 Worked on the Bracket for the RX64 and robot assembly
    [RX_64.SLDPRT, bracketRx64.SLDPRT, linkShoulder.SLDPRT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]
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2019-11-15 Final Support and Motor Gear
    I removed old files off of my branch.
    [Final_motorGear.SLDPRT, Final_supportGear.SLDPRT, Final_supportGear_motorGear.SLDASM]
2019-11-15 Remove_old_Files
    I removed old files so that files can easily be found.
    [V4_motor_gear_shaft.SLDPRT, V4_support_gear_revised.SLDPRT, V5_motorGear.SLDPRT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]
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2019-11-15 The correct motor gear shaft was created.
    I adjusted the length of the shaft connected to the motor gear.
    [Final_motorGear.SLDPRT]
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2019-11-20 Update BaseGearShaft.SLDPRT
    Diameter was changed from 70 mm to 68 mm
    [BaseGearShaft.SLDPRT]
2019-11-20 Shoulder Gear Error
    Fillet was added to the BaseGearShaft
    [BaseGearShaft_Fillet.SLDPRT, Temporary.SLDASM, shoulder_gear.SLDPRT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]
2019-11-20 Shoulder Gear Hole
    A hole was added to the shoulder gear to loop wires through
    [BaseGearShaft_Fillet.SLDPRT, link_gear.SLDASM, shoulder_gear.SLDPRT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]
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2019-11-26 new gear without inset feature
    This gear doesn't use the inset feature. This solves the problem of having 2 seperated files for printing and assembly. This will also allow us to mess with the tolerances.
    [shoulder_gear_original_optional.SLDPRT]
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2019-11-26 new shaft with fillet and correct dimensions
    [BaseGearShaft_Fillet.SLDPRT]
2019-11-26 rename to reflect the correct file
    [shoulder_gear_noInset.SLDPRT]
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2019-11-26 new design for mounting the gear to the link
    [Link1_gearMounting.SLDPRT]
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2019-11-27 fixed shoulder gear
    [shoulder_gear_noInset.SLDPRT]
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2019-12-09 new gear shaft with better tolerances
    [gearShafv2.STL]
2019-12-09 change tolerances
    [shoulder_gear_noInset.SLDPRT]
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2019-12-10 change some tolerances
    [Link1_gearMounting.SLDPRT]
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2019-12-10 update some tolerances
    [link_gear_shaft.SLDPRT]
2019-12-12 adjusting the link tolerances
    [armFullAssembled.SLDASM]
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2020-06-21 redesign the base
    [base_v2.SLDPRT]
2020-06-21 add subassembly for the AX12 and the bracket
    [A12_bracket_subassm.SLDASM]
2020-06-21 add STL and gcode files for printing the bracket
    [AX12_bracket_v2.STL]
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2020-06-22 stl file for part 1 of the base
    [newBase_p1.STL]
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
